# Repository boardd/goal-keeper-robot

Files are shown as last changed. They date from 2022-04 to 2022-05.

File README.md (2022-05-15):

# Autonomous Goal Keeper

## The Project

The aim of this project was to create a robot that can autonomously detect a "soccer ball" and defend a goal. We aimed to use computer vision for ball tracking and popular control methods such as PID and LQR to accurately position the robot's arm. After considering the relevant constraints such as time and cost, we decided to build a scale model of the setup so we can demonstrate the core capabilities of our robot without building a full scale version.

## The Robot

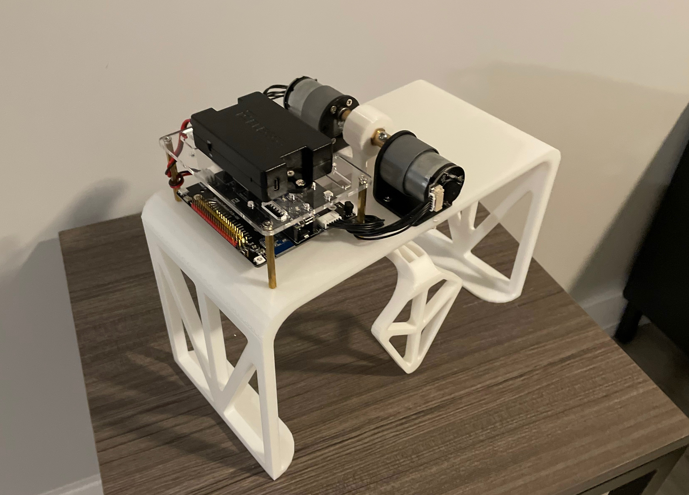
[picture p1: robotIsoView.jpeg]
Robot Isometric View


## The Hardware

The robot was constructed using 3D-Printed parts as this was the most efficient way for us to prototype and manufacture the robot. At first we wanted to use a stick shaped goalie to block balls but found that this would perform poorly for several reasons. A thin stick shaped goalie would require much more precise inverse kinematics which would be difficult for a project with such a short time frame. We would need a lot of control over the arm which would be difficult given the inconsistencies that could be present with our computer vision algorithm. A rectangular goal also proved difficult to cover for a single linked revolute arm as it only moves in one dimension, but needs to be able to defend the xy-plane formed by the front face of the robot. We eventually arrived at the design as shown in the picture below, which allowed us to cover the entire goal, including all of the corners. The goalie blocker also has cutouts so that we are able to optimize the rotational inertia and achieve larger accelerations by the motor.

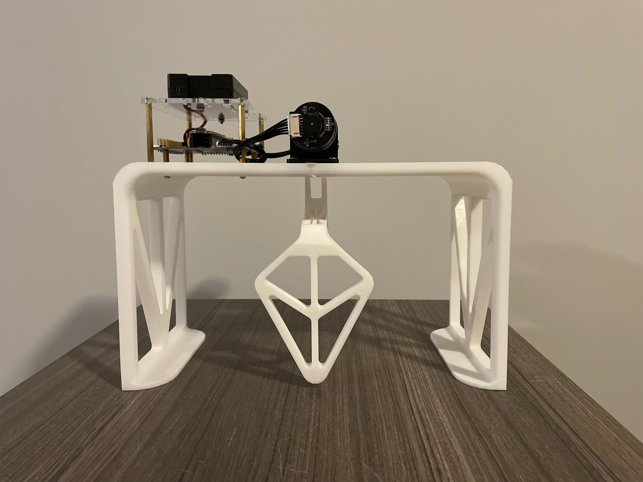
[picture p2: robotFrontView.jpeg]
Robot Front View


Most of the mounting hardware was recycled from the <a href="https://www.elegoo.com/collections/robot-kits/products/elegoo-tumbller-self-balancing-robot-car">Elegoo Tumbller</a>, which was the robot we used in labs in the past. This included 8 standoffs, 2 motor mounts, one plastic plate, and a few M3 screws. Although we designed the goal to be printed in 2 parts and glued together, we also used the motor mounts to strengthen the bridging by screwing it between the two halves. By mounting all of the hardware on top of the robot, we make the robot portable and easy to relocate to anywhere it might need to be. The two motors are set up in a counter-rotating configuration so that we are able to maximize the amount of availiable torque whilst still maintaining the maximum speed that we are able to reach. We chose to direct drive the motors as it was the most robust and simple design to implement given the time constraints.

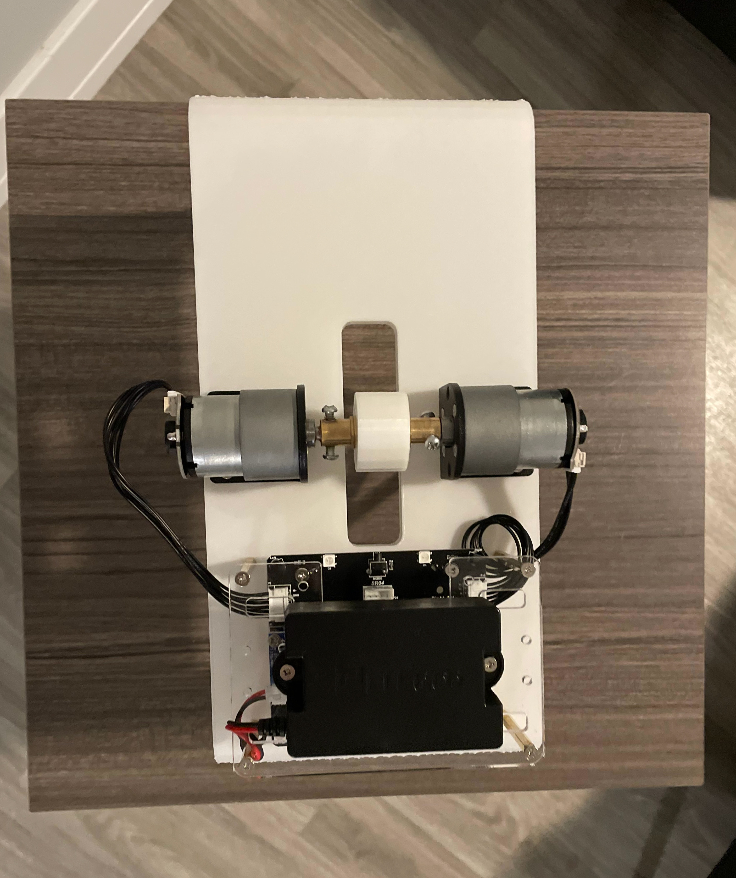
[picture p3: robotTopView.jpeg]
Robot Top View


### Electronics

The electronics of the robot are also mostly recycled from the Elegoo Tumbller. We used an Arduino Nano microcontroller to recieve and command joint positions to the two motors that came with the Elegoo kit. The motors have encoders which have 1560 ticks per revolution, enough resolution to allow us to have relatively high precision on the position of the motor. We also used the battery from the Elegoo kit to power our whole setup. A close up of our electronics is below.

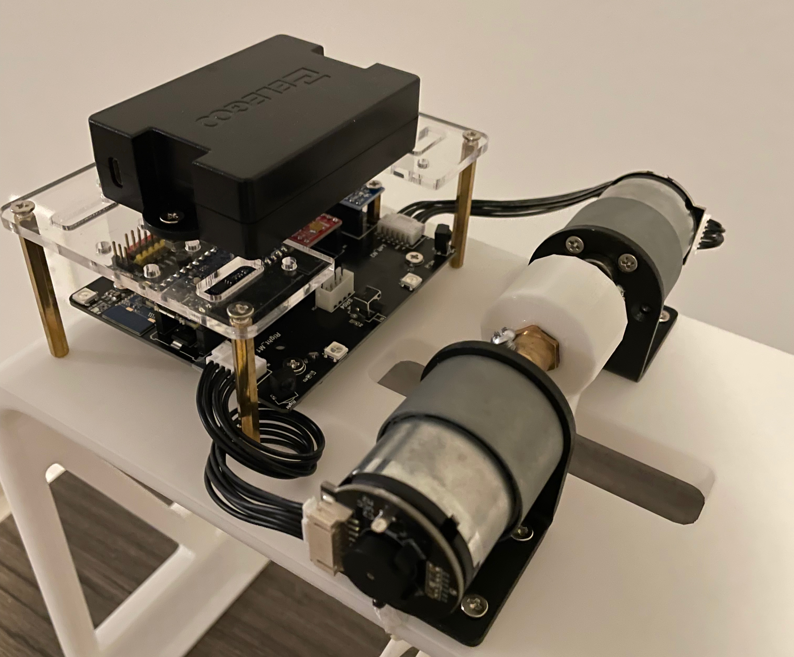
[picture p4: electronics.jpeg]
Electronics


Additionally, we used a camera rigged to provide a top view of the course as shown below. The camera uses a global shutter to minimize distortion and runs at roughly 37 fps. You can get the same camera <a href="https://www.amazon.com/Global-Shutter-Monochrome-Cameras-Windows/dp/B089QFRTVX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">here</a>, though we do recommend a different camera with a higher framerate if you able to get one. We light the scene using several lamps. This gives us much more controllable lighting conditions for thresholding in our computer vision.

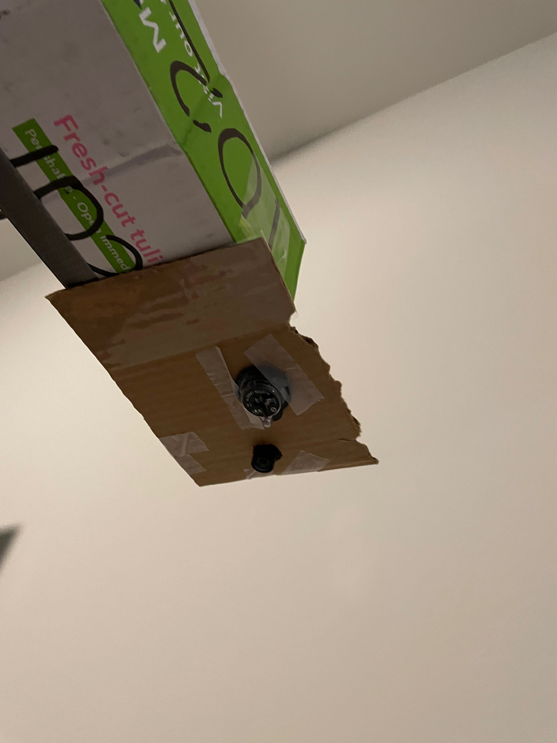
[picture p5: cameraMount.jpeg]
Camera Mount


### The Setup

We built the majority of the setup using cardboard. We first started by covering a large piece of cardboard with white paper to help our vision system more easily identify the ball. In hindsight, we would have used a color camera rather than a monochrome one as this made detecting the orange colored ping pong ball more difficult. We placed the camera roughly 5 feet above the ground so it is able to see most of the setup. We placed 4 ArUco markers in the corners of a rectangle to help our computer vision algorithm determine the location of the ball. Below are two pictures showing the full setup and what the view from the camera is roughly like (note that this was taken using a cell phone camera).

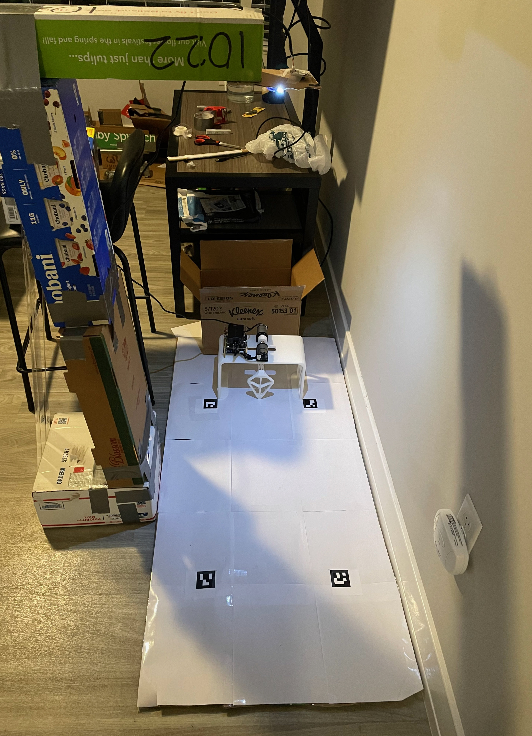
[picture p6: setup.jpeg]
Full Setup
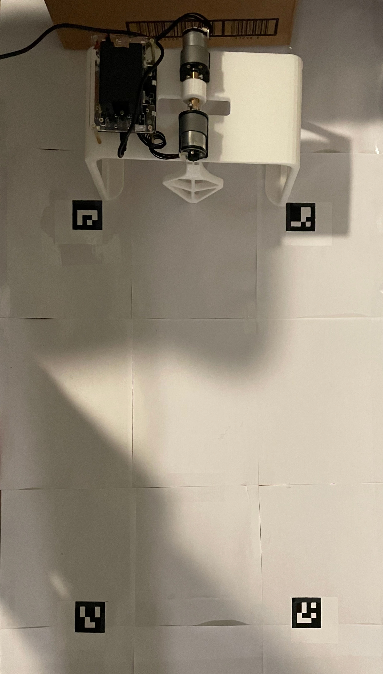
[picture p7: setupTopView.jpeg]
Top View of Setup
 

### Robot Dimensions

All dimensions are in millimeters.

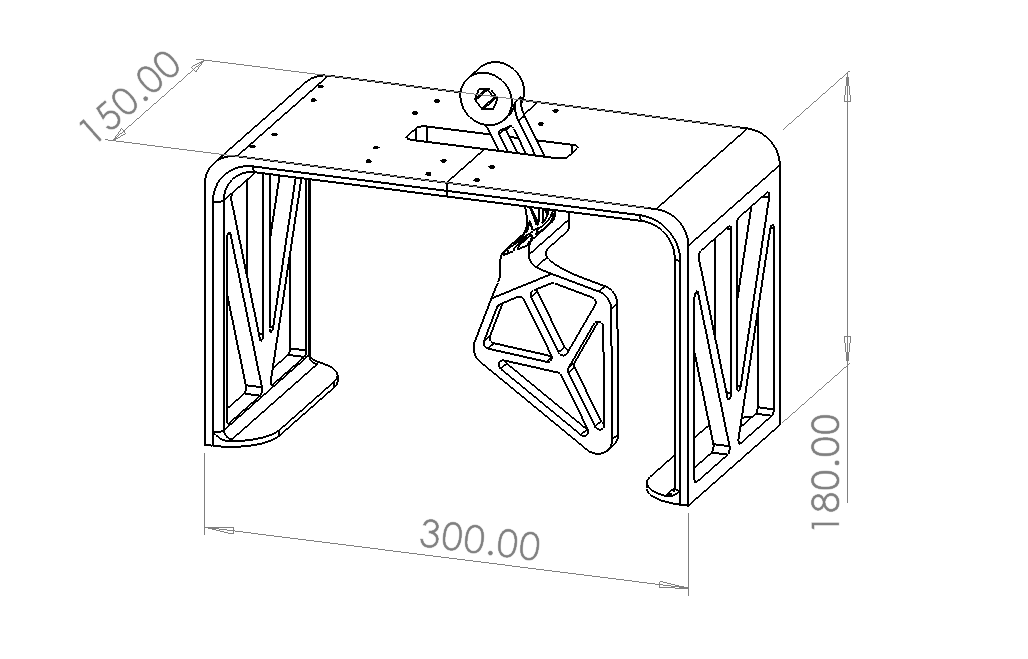
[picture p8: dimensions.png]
Robot Dimesions


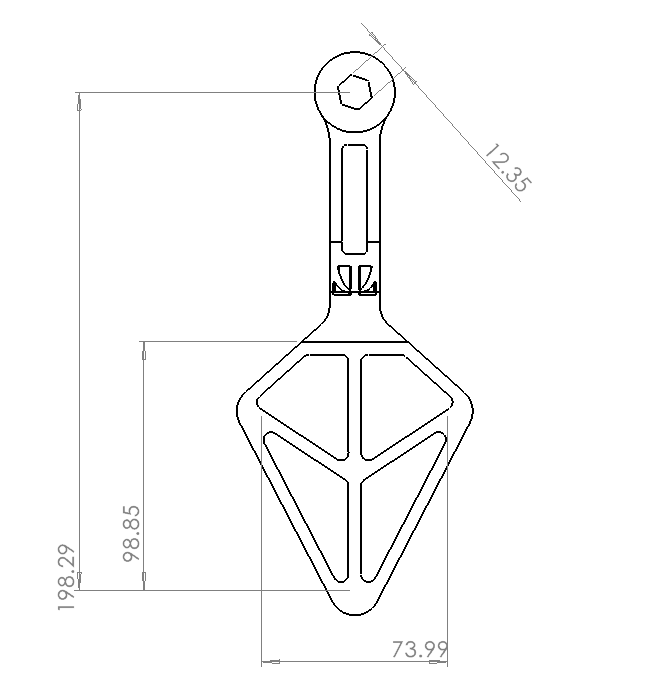
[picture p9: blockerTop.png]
Blocker Top Dimensions
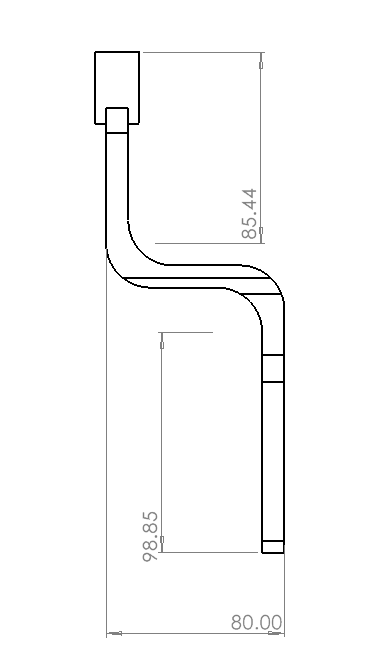
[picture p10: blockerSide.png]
Blocker Side Dimensions
 

### Robot CAD

All robot CAD is available on our github for 3D-printing (STL files only)

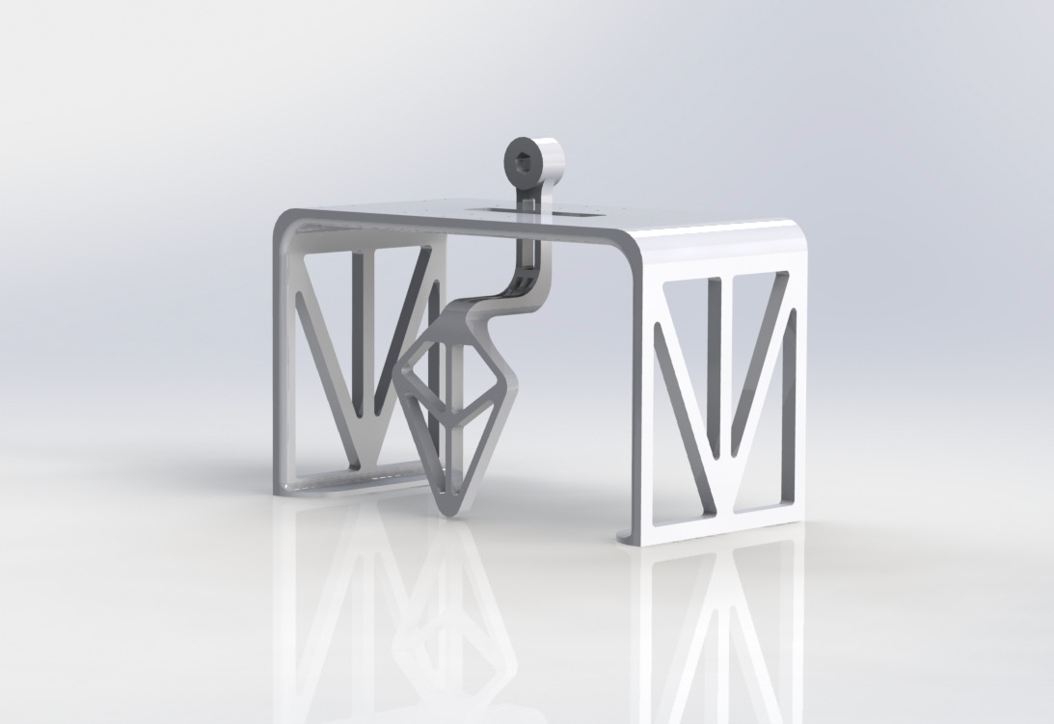
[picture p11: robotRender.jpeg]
robot render


### Parts Used

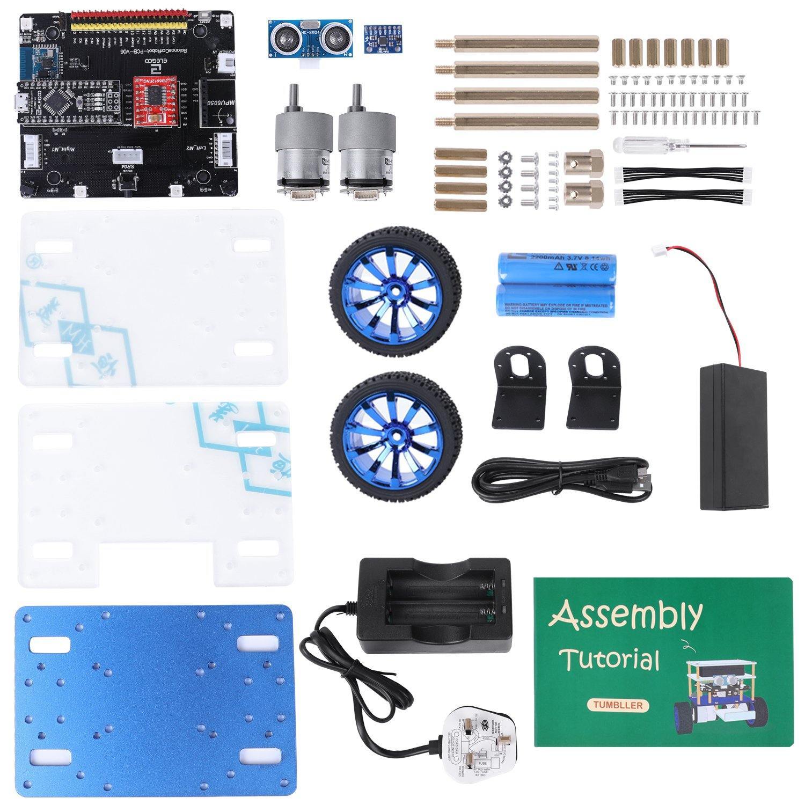
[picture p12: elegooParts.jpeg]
elegooParts
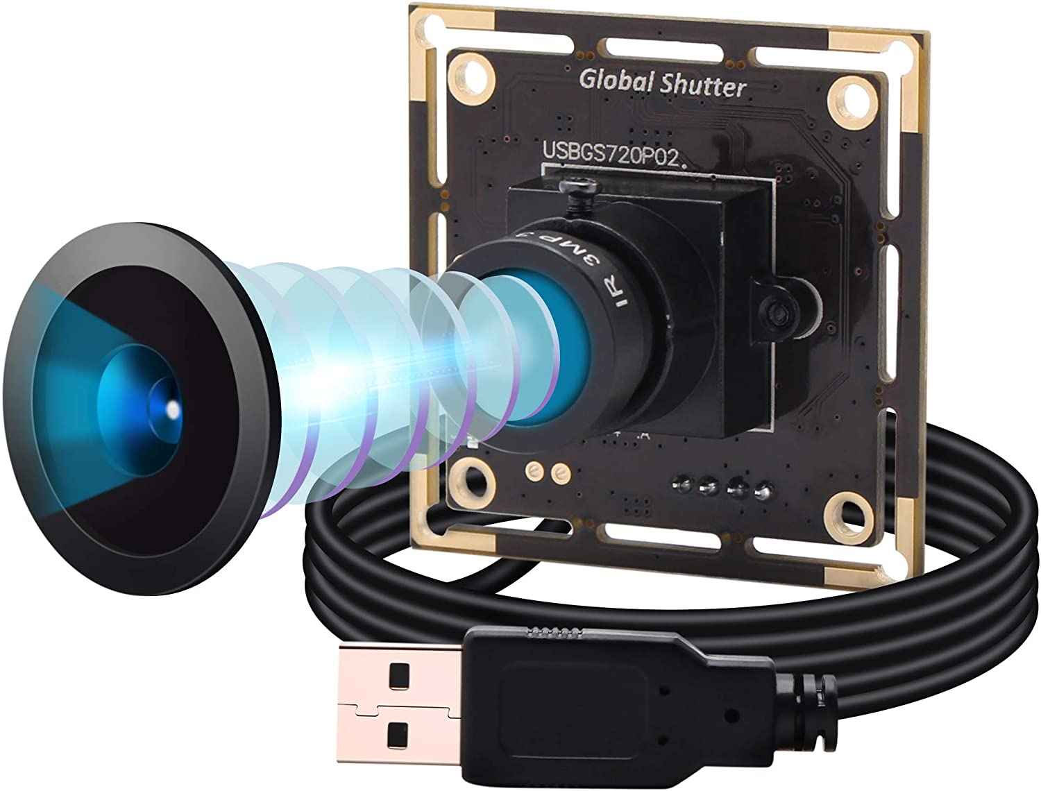
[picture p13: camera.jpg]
camera
 

## The Software

### Tracking the Ball

To compute the angle at which we should position the arm to block the ball, we need to know where the ball is going to end up in the horizontal direction, once it reaches the goal.

#### Finding the ball

We determine the location of the ball using a top down camera over the playing field. The raw images look like the following:

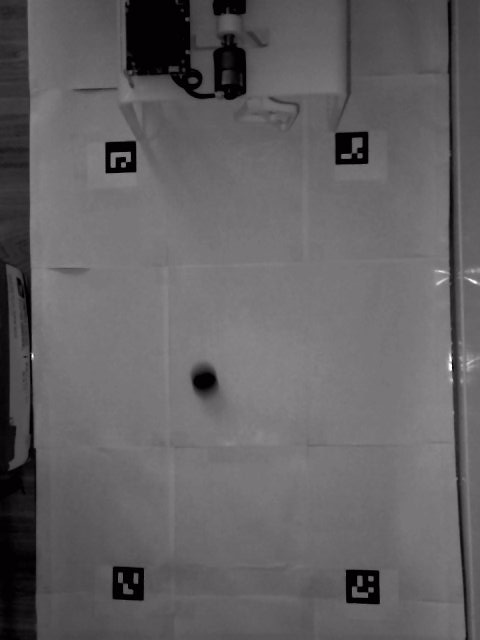
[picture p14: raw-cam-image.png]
Raw image from the camera


We painted the ball black to give it high contrast against the white playing field, which makes it easier to identify with computer vision. If you are not using a monochromatic camera like we did, you should be able to leave the ball its original color (orange) and you will find it much easier to threshold based on RGB or HSV values.

We use OpenCV to apply an adaptive gaussian threshold to the image, which yields the following:

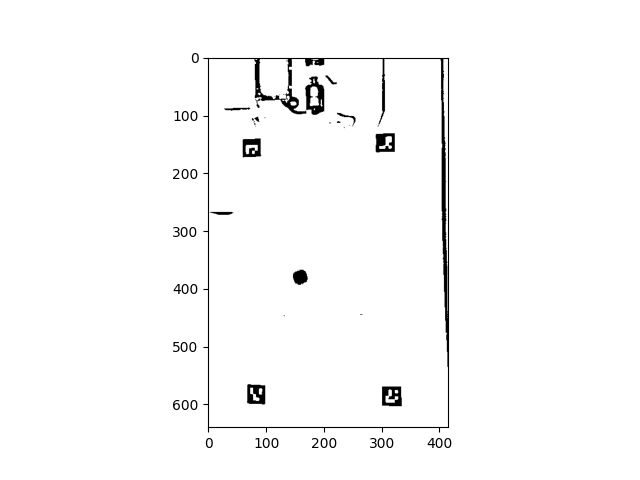
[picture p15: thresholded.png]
Thresholded image


We can then use OpenCV's contour detection to find contiguous regions of black pixels. We filter these contours by area, keeping only the ones within a pre-defined range. This helps us ignore contours that are too large or too small and reduces the number of false positives.

#### Computing the ball's position

Once we have identified one or more contours in the image, we can compute the position of each of these contours relative to the ArUco markers on the field, which are at known positions. We do so by using OpenCV's built-in ArUco marker detector. We can then compute a transformation from image space to world space and apply it to all of the identified contours.

Once we know the location of the contours in the real world, we can further filter them to exclude any which are not inside the rectangle defined by the markers. This reliably produces only a single location, corresponding to the ball.

In the following images, we draw a red rectangle with its center on where we believe the ball to be:

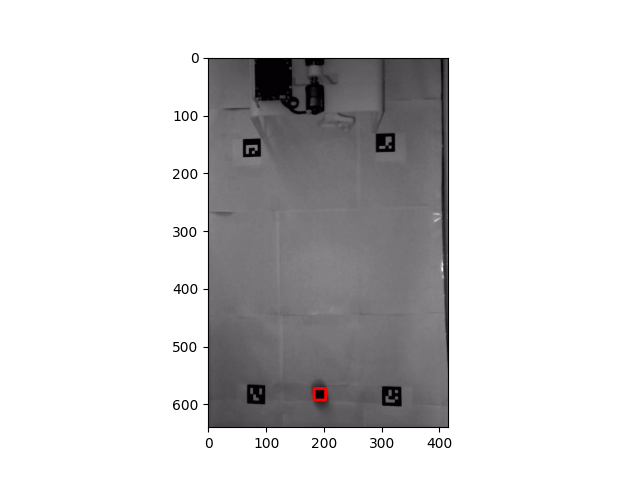
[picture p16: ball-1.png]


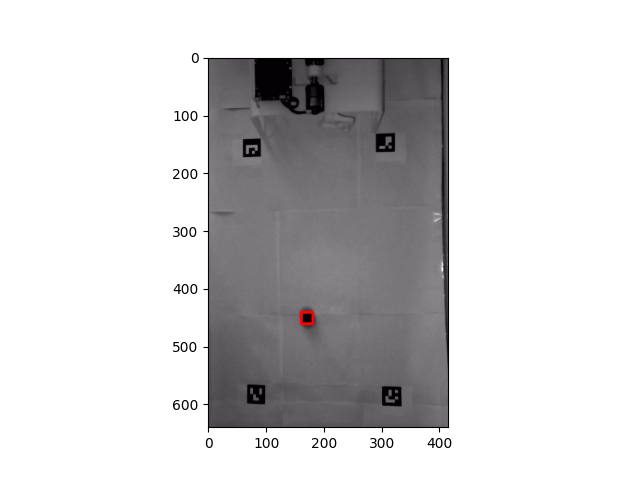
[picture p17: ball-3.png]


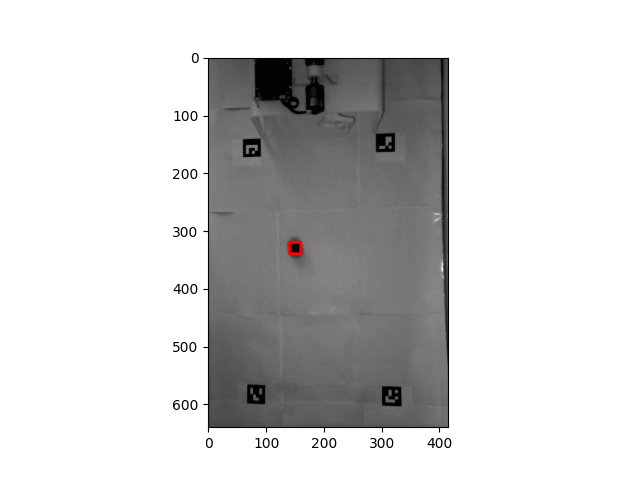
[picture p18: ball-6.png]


#### Estimating the ball's trajectory

Once we have the position of the ball over several frames, we can estimate its trajectory in order to predict where it will end up when it reaches the goal. If we only have a single frame of the ball so far, we simply use its x-coordinate in world space. Otherwise, we take up to the last 5 positions of the ball, and for each subsequent pair of positions, compute the velocity of the ball in world space. We take the average of these velocities, then solve for the ball's x-coordinate at the time that it would reach the y-coordinate of the goal. The following video visualizes this computation:

<iframe width="560" height="315" src="https://www.youtube.com/embed/EhwE5aTzZk0" title="YouTube video player" frameborder="0" allow="accelerometer; autoplay; clipboard-write; encrypted-media; gyroscope; picture-in-picture" allowfullscreen></iframe>

### LQR Control

We control the arm with an LQR controller, using the following linear model of the dynamics. Constant c0 represents a friction term, and constant c1 represents the impact of the control sent to the motor on its velocity.

A Matrix

B Matrix

We collected data by sending a sequence of commands to the robot and measuring the resulting angles over time. We then tuned constants c0 and c1 to match this data, which yielded c0=.03, c1=.00285. The following is a plot comparing the actual encoder data after a sequence of commands with a simulation using the above model and parameters.

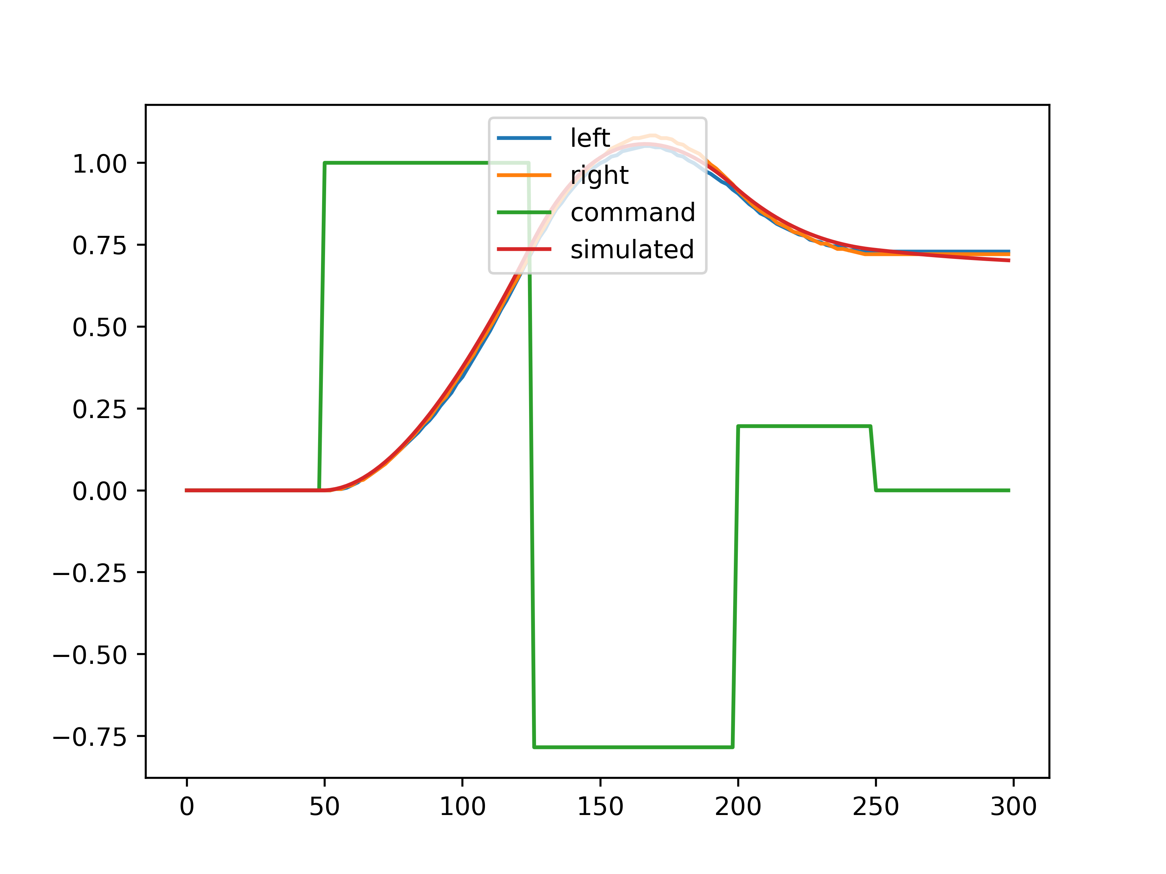
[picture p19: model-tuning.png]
Graph of model tuning vs real data


### Communication

Since the arm of the goal keeping robot is controlled by an arduino, it cannot read the images from the camera directly. Instead, our computer vision algorithm runs on a laptop connected to the USB camera as well as the arduino, over serial. The laptop reads images from the camera, computes the location of the ball on the board, computes the angle at which the arm should be set, and finally sends that desired angle over the serial port to the arduino. We used pyserial to establish the serial communications between the arduino and the computer. Upon receiving an update, the arduino LQR controller issues commands to the motors to achieve the desired angle.

## Performance Demonstrations

Below are some youtube videos showing how our robot performs under different circumstances.

### Ball on Stick

<iframe width="560" height="315" src="https://www.youtube.com/embed/wQ2Xh3evgs4" title="YouTube video player" frameborder="0" allow="accelerometer; autoplay; clipboard-write; encrypted-media; gyroscope; picture-in-picture" allowfullscreen></iframe>

### Without trajectory estimation

<iframe width="560" height="315" src="https://www.youtube.com/embed/va0qUtZI4oE" title="YouTube video player" frameborder="0" allow="accelerometer; autoplay; clipboard-write; encrypted-media; gyroscope; picture-in-picture" allowfullscreen></iframe>

### With trajectory estimation

<iframe width="560" height="315" src="https://www.youtube.com/embed/xyy4dbmpT3A" title="YouTube video player" frameborder="0" allow="accelerometer; autoplay; clipboard-write; encrypted-media; gyroscope; picture-in-picture" allowfullscreen></iframe>

## Problems Faced

### Communication

#### The Problem

One issue we faced is that when we rapidly sent updates to the desired angle to the LQR controller, we observed unpredictable behavior. The following is a video in which we sent updates with a 0.2s delay in-between. The robot behaved as expected:

<iframe width="560" height="315" src="https://www.youtube.com/embed/YelFhvKkZ9k" title="YouTube video player" frameborder="0" allow="accelerometer; autoplay; clipboard-write; encrypted-media; gyroscope; picture-in-picture" allowfullscreen></iframe>

However, if we sent updates more rapidly, the controller behaved unexpectedly. The following is a video in which we sent the updates with a 0.1s delay:

<iframe width="560" height="315" src="https://www.youtube.com/embed/VBRqGhC0dmI" title="YouTube video player" frameborder="0" allow="accelerometer; autoplay; clipboard-write; encrypted-media; gyroscope; picture-in-picture" allowfullscreen></iframe>

#### The Solution

Initially, we thought this may be a quirk of the LQR controller which we were using. However, it turned out that as we sent several updates over serial in rapid succession, the messages would be read simultaneously on the Arduino side. This yielded a garbled desired angle, which caused the unpredictable behavior. We solved the issue by separating each update to the arduino with a line break '\n'. On the Arduino side, we could then use the Serial.readStringUntil('\n') method to isolate each update appropriately.

### Lag

#### The Problem

As with any digital system, there is significant latency from the balls motion in the real world to the camera producing an image, to the computer vision system producing a position, and to the arduino finally positioning the arm. This sequence of delays meant that the arm could not quite keep up with the ball, which caused the arm to miss if the ball was travelling diagonally.

#### The Solution

As discussed above, the solution to this problem was to rely not on our computation of where the ball is currently, but to also predict where the ball will be in the future. Although the system is not able to react any faster, it can make a smarter decision on where to position the arm. Adding trajectory estimation increased the success rate of the arm from around 60% to more than 95%.

## Future Work

### 3D

Currently, the goal keeper only operates in two dimensions. It has no knowledge of the ball's height relative to the ground. With an additional camera looking at the board sideways, we could incorporate this information to better inform the arm's position.

### Scale

Bigger is better. We chose to make a relatively small robot for the sake of simplicity given the limited time we had to develop the system. A larger robot (even full-scale) would of course introduce challenges with safety, overcoming inertia, and overcoming additional inaccuracies given a smaller margin of error.

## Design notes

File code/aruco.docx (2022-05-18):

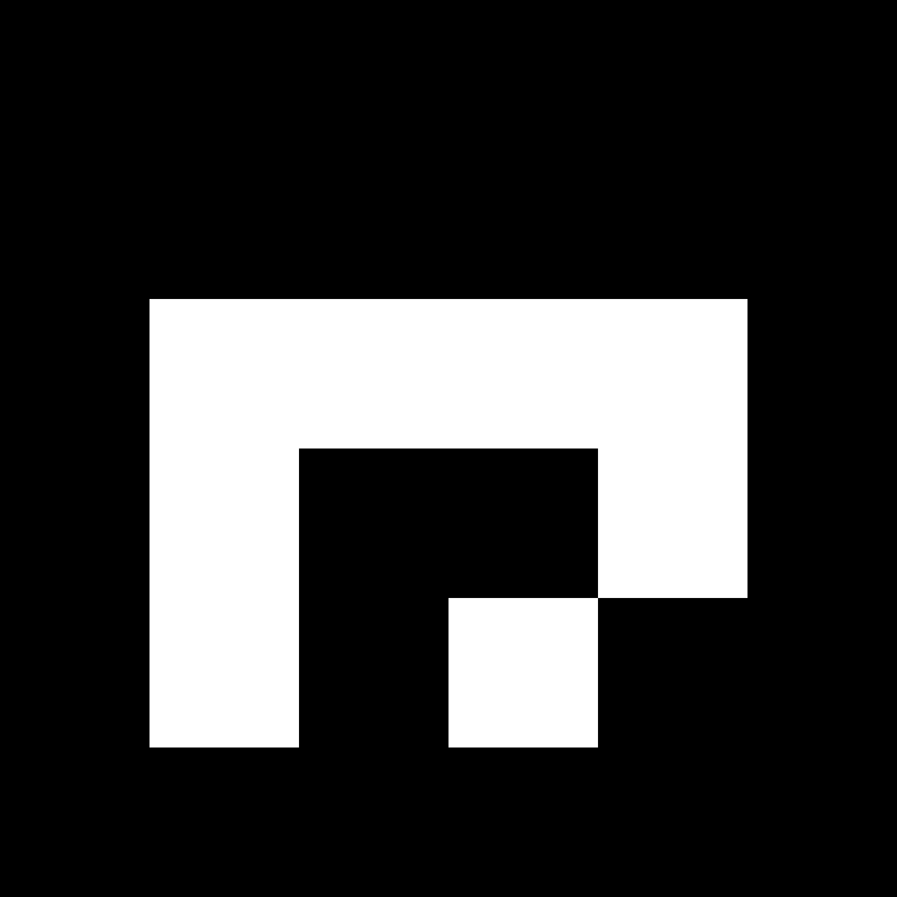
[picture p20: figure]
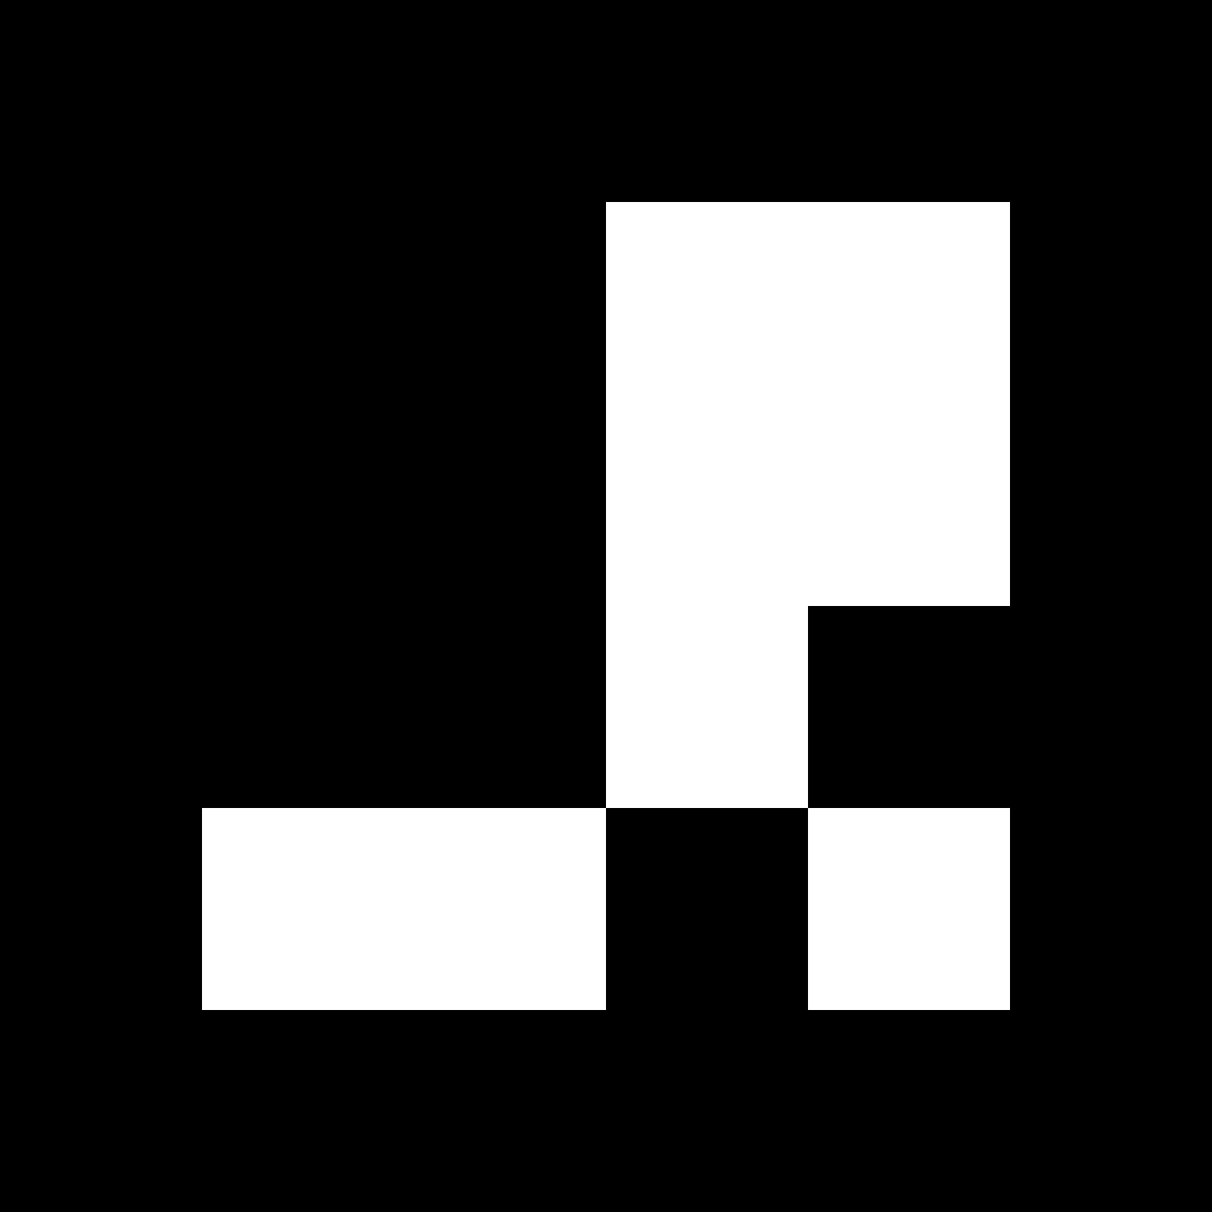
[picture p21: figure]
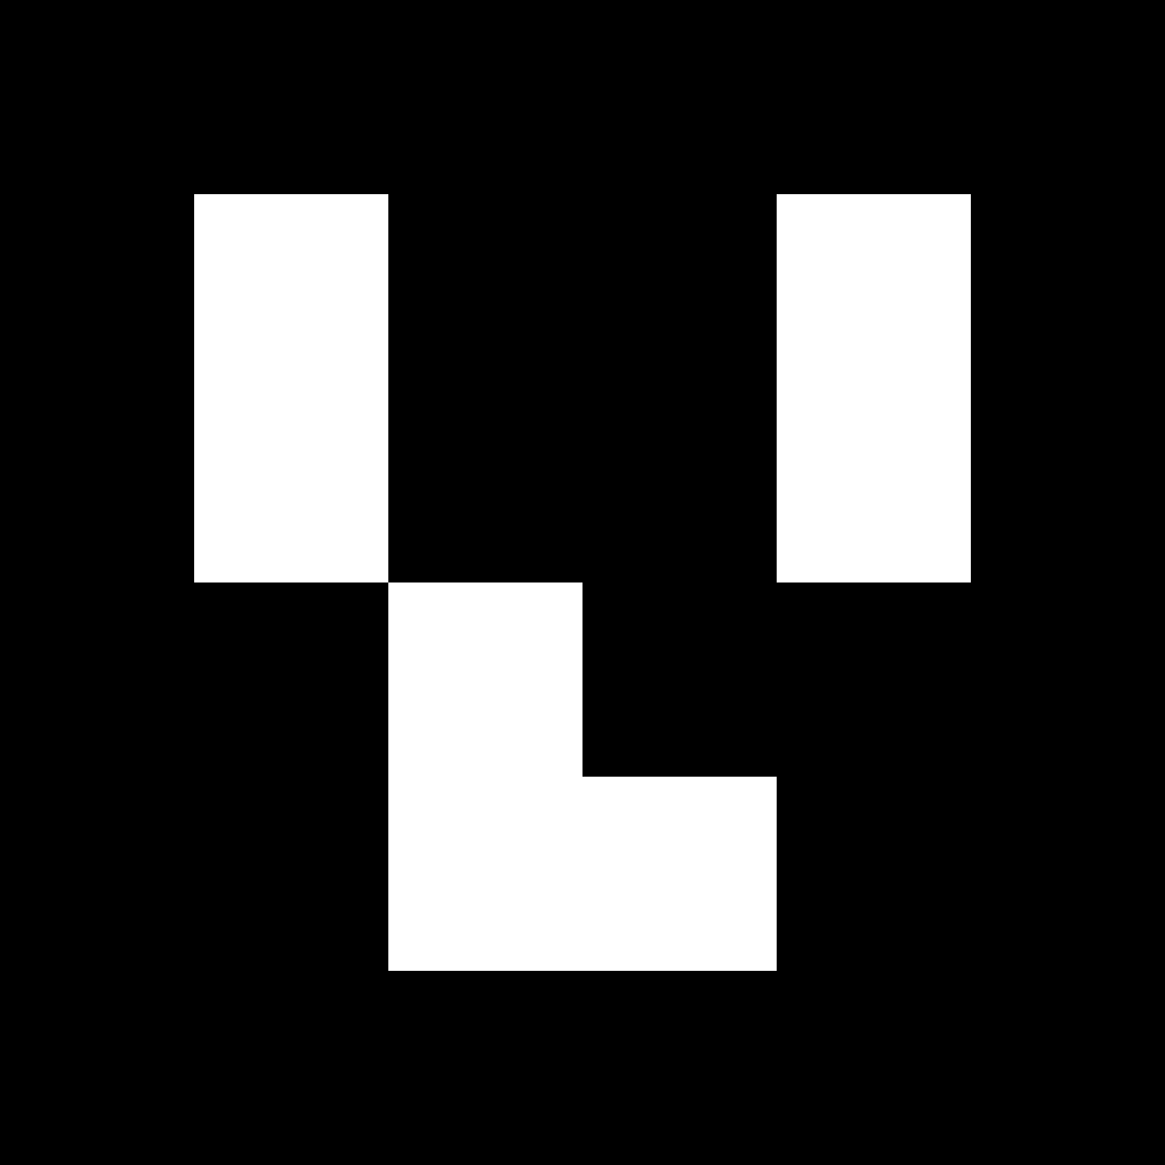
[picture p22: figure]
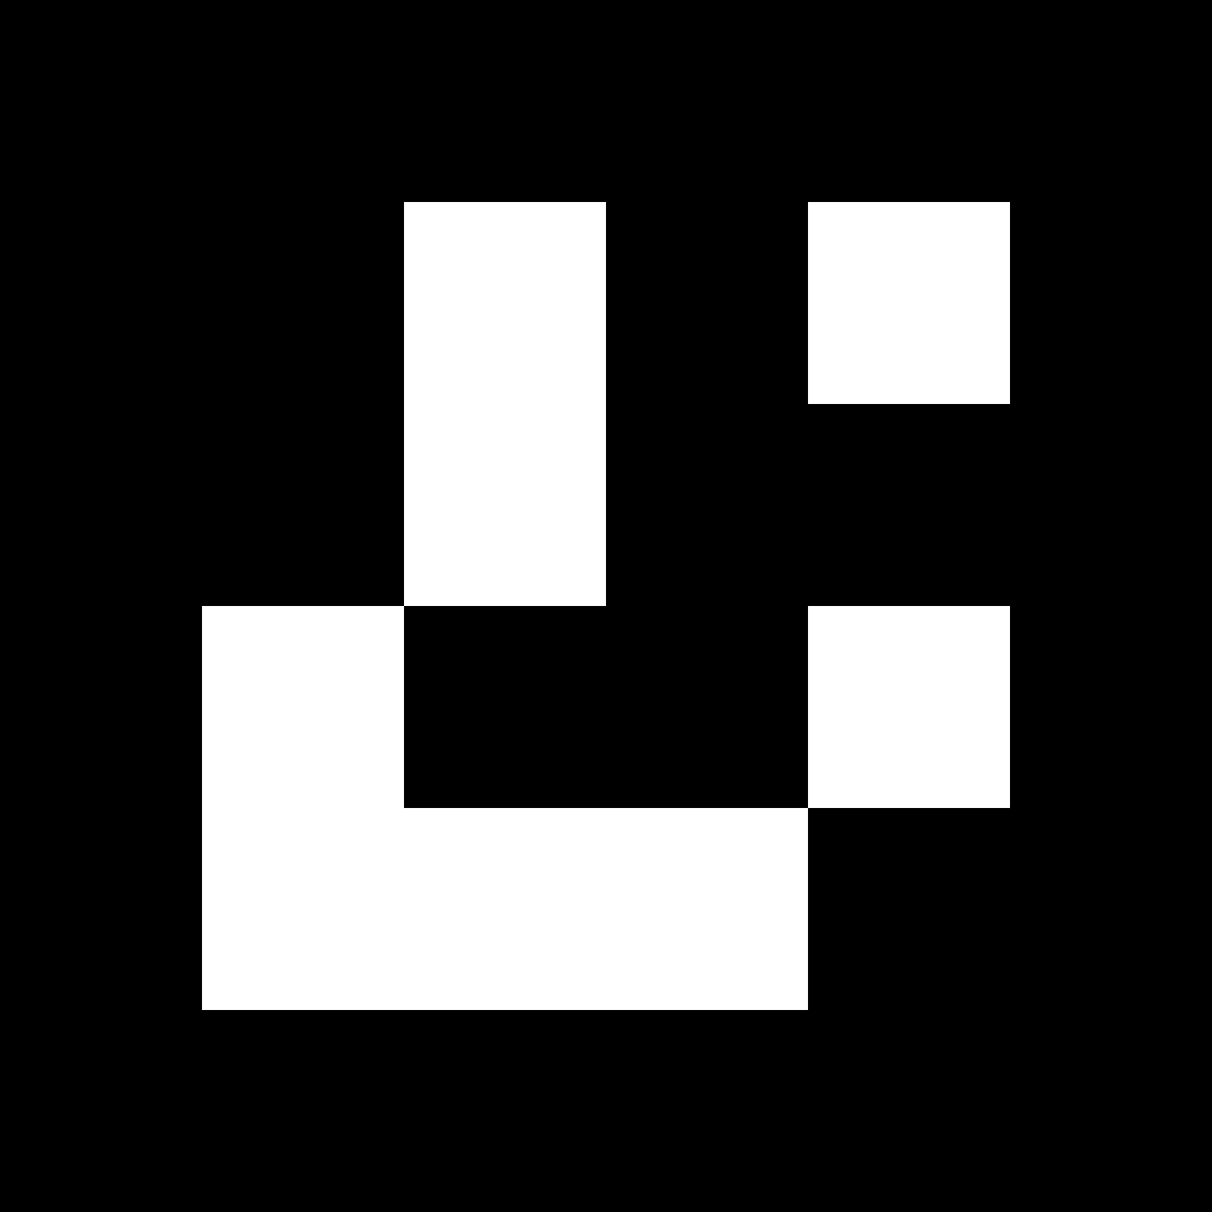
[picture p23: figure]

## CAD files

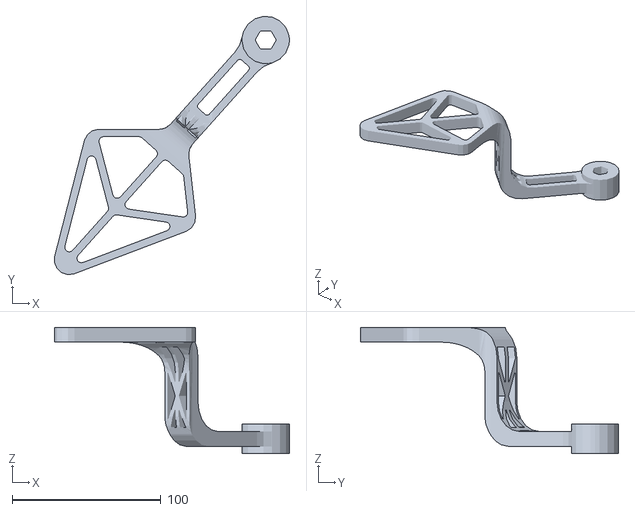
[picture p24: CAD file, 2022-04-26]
Printable Files/blocker arm.STL
158.0 x 173.7 x 85.0

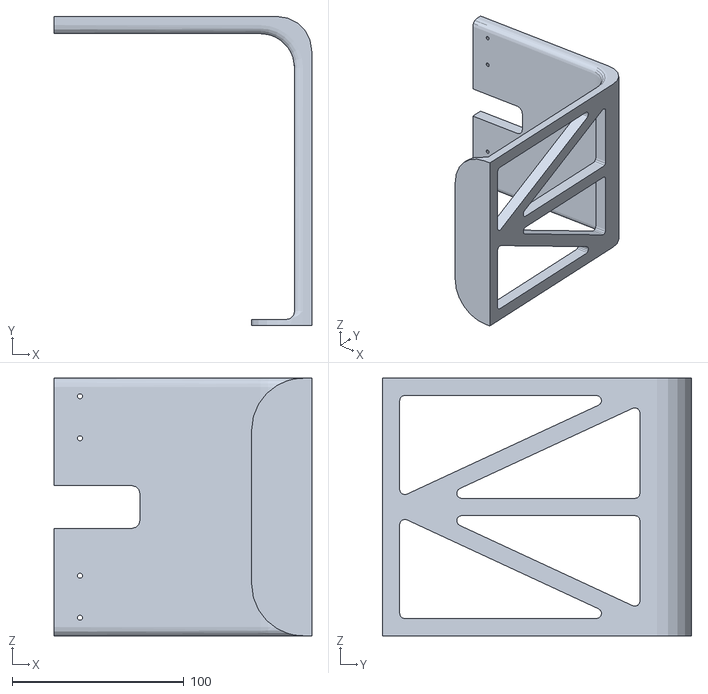
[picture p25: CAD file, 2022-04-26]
Printable Files/goal-right.STL
150.0 x 180.0 x 150.0

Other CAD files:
Printable Files/goal-left.STL

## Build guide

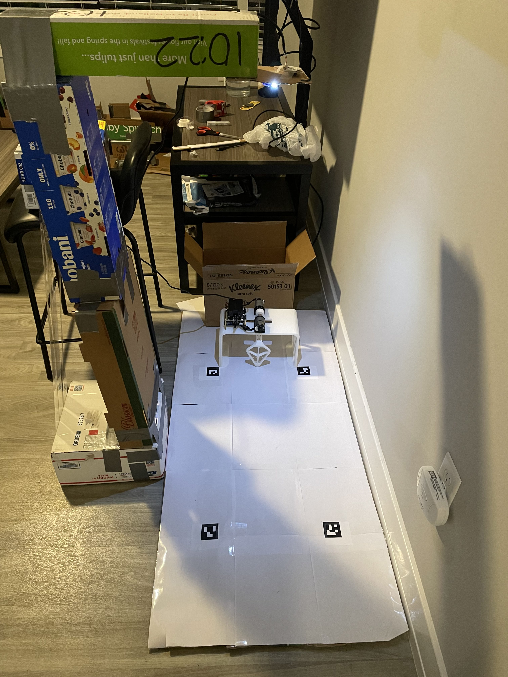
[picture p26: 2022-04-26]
setup.jpg

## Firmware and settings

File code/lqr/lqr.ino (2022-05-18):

/******************************************************************/

#include "my_encoders.h"
#include "Motor.h"

/******************************************************************/

Motor Motor;

void setup()
{
  Serial.begin( 1000000 );
  while ( !Serial ) {};
  Serial.setTimeout(100);
  Motor.Motor_init();
  Encoder_init( &(Motor.left_angle), &(Motor.right_angle) );
}

float k1 = 960;
float k2 = 28.5;
float ts = 0.002;
float MAX_ANGLE = 0.6;

/******************************************************************/

bool VERBOSE = false;
unsigned long start_micros = -1;
unsigned long timestep_micros = 2000;
unsigned long next_timestep_micros = -1;

void loop()
{
  Encoder_init( &(Motor.left_angle), &(Motor.right_angle) );
  start_micros = micros();
  next_timestep_micros = 0;
  float previous_angle_radians = 0;
  float desired_angle_radians = 0;
  Serial.println("READY");
  while (true) {
    if ( Serial.available() > 0 ) {
      String s = Serial.readStringUntil('\n');
      char *cmd = s.c_str();
      if (VERBOSE) {
        Serial.print("Received: ");
        Serial.println(cmd);
      }
      if (cmd[0] == 'v') {
        VERBOSE = !VERBOSE;
      } else {
        desired_angle_radians = atof(cmd);
        if (desired_angle_radians > MAX_ANGLE) {
          desired_angle_radians = MAX_ANGLE;
        }
        if (desired_angle_radians < -MAX_ANGLE) {
          desired_angle_radians = -MAX_ANGLE;
        }
      }
    }

    unsigned long current_micros = micros();
    unsigned long elapsed_micros = current_micros - start_micros;
    unsigned long elapsed_millis = elapsed_micros / 1000;

    // Timekeeping
    if (elapsed_micros < next_timestep_micros) {
      continue;
    }
    next_timestep_micros += timestep_micros;

    // Read encoders
    Read_encoders( &(Motor.left_angle), &(Motor.right_angle) );

    // Compute angle and velocity
    float current_angle_encoder = ((float)Motor.left_angle + (float)Motor.right_angle) / 2.0;
    float current_angle_radians = current_angle_encoder / 780.0 * PI;
    float current_velocity_radians = (current_angle_radians - previous_angle_radians) / ts;
    previous_angle_radians = current_angle_radians;

    // Do LQR
    float desired_velocity = 0;

    float current_error_radians = desired_angle_radians - current_angle_radians;
    float current_velocity_error = desired_velocity - current_velocity_radians;

    long command = k1 * current_error_radians + k2 * current_velocity_error;

    // Safety
    if (command > 255) {
      command = 255;
    }
    if (command < -255) {
      command = -255;
    }

    // Logging
    if (VERBOSE) {
      Serial.print("elapse:");
      Serial.println(elapsed_micros);
      Serial.print("angle:");
      Serial.println(current_angle_radians);
      Serial.print("vel:");
      Serial.println(current_velocity_radians);
      Serial.print("des angle:");
      Serial.println(desired_angle_radians);
      Serial.print("des vel:");
      Serial.println(desired_velocity);
      Serial.print("cmd:");
      Serial.println(command);
      Serial.println("-----");
    }

    Motor.Left_command(command);
    Motor.Right_command(command);
  }

  Motor.Stop();
}

/******************************************************************/

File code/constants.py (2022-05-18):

ARM_HEIGHT = 8 + (3 / 8)  # inches

AREA_MIN = 400
AREA_MAX = 1200

EXPECTED_HEIGHT_OVER_WIDTH = 1
MAX_HEIGHT_OVER_WIDTH_ERROR = 2

# Aruco marker positions
# 1 2
# 3 4
ARUCO_MARKER_SIZE = 2  # width/height, inches
BOARD_WIDTH = 14  # Distance between centers horizontally, inches
BOARD_HEIGHT = 26  # Distance between centers vertically, inches
BOARD_MARGIN = ARUCO_MARKER_SIZE / 2

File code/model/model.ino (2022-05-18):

/******************************************************************/

#include "my_encoders.h"
#include "Motor.h"

/******************************************************************/

#define TARGET 500

/******************************************************************/

Motor Motor;

static bool go = false;  /* motor enable */

/******************************************************************/

void setup()
{
  Serial.begin( 1000000 );
  while( !Serial ){};
  delay( 1000 ); // Delay to make sure above message prints out.
  Motor.Motor_init();
  Serial.println( "Motor.Pin_init done." );
  Serial.println( "If we hang here power cycle the robot. Expect more printout" );
  delay( 1000 ); // Delay to make sure above messages print out.
  Encoder_init( &(Motor.left_angle), &(Motor.right_angle) );
  Serial.println( "Encoder_init done." );
  Serial.println( "Wheels should be off the ground."  );
  Serial.println( "Type g <return> to run test, s <return> to stop."  );
  Serial.println( "Typing window is at the top of the serial monitor window" );
}

/******************************************************************/

// Take user input
void ProcessCommand()
{

  if ( Serial.available() <= 0 )
    return;

  int c = Serial.read();
  switch (c)
    {
      case 'S': case 's':
        Serial.println( "Stop!" );
        go = false;
        break;
      case 'G': case 'g':
      Serial.println( "Go!" );
        go = true;
        break;
      default:
        break;
    }
}

/******************************************************************/

unsigned long start_micros = -1;
unsigned long timestep_micros = 2000;
unsigned long next_timestep_micros = -1;

void loop()
{
  if (!go) {
    start_micros = -1;
    next_timestep_micros = -1;
    Motor.Stop();
    ProcessCommand();
    return;
  }

  if (start_micros == -1) {
    start_micros = micros();
    next_timestep_micros = 0;
  }

  unsigned long current_micros = micros();
  unsigned long elapsed_micros = current_micros - start_micros;
  unsigned long elapsed_millis = elapsed_micros / 1000;

  // Reset
  if (elapsed_millis >= 300) {
    Encoder_init( &(Motor.left_angle), &(Motor.right_angle) );
    go = false;
    Motor.Stop();
    return;
  }

  if (elapsed_micros < next_timestep_micros) {
    return;
  }
  next_timestep_micros += timestep_micros;  

  int command = 0;

  if (elapsed_millis >= 0) {
    command = 0;
  }
  if (elapsed_millis >= 50) {
    command = 255;
  }
  if (elapsed_millis >= 125) {
    command = -200;
  }
  if (elapsed_millis >= 200) {
    command = 50;
  }
  if (elapsed_millis >= 250) {
    command = 0;
  }

  Motor.Left_command( command );
  Motor.Right_command( command );

  Read_encoders( &(Motor.left_angle), &(Motor.right_angle) );

  Serial.print(elapsed_millis);
  Serial.print(",");
  Serial.print(Motor.left_angle);
  Serial.print(",");
  Serial.print(Motor.right_angle);
  Serial.print(",");
  Serial.print(command);
  Serial.println("");
}

/******************************************************************/

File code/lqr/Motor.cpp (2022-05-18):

#include <Arduino.h>
#include "Motor.h"

/* Motor pins */
#define AIN1 7
#define PWMA_LEFT 5
#define BIN1 12
#define PWMB_RIGHT 6
#define STBY_PIN 8

void Motor::Motor_init()
{
  pinMode(AIN1, OUTPUT);
  pinMode(BIN1, OUTPUT);
  pinMode(PWMA_LEFT, OUTPUT);
  pinMode(PWMB_RIGHT, OUTPUT);
  digitalWrite(AIN1, HIGH);
  digitalWrite(BIN1, LOW);
  analogWrite(PWMA_LEFT, 0);
  analogWrite(PWMB_RIGHT, 0);
  pinMode(STBY_PIN, OUTPUT);
  digitalWrite(STBY_PIN, HIGH);
}

void Motor::Stop()
{
  digitalWrite(AIN1, HIGH);
  digitalWrite(BIN1, LOW);
  analogWrite(PWMA_LEFT, 0);
  analogWrite(PWMB_RIGHT, 0);
}

void Motor::Forward(int speed)
{
  digitalWrite(AIN1, 0);
  digitalWrite(BIN1, 0);
  analogWrite(PWMA_LEFT, speed);
  analogWrite(PWMB_RIGHT, speed);
}

void Motor::Back(int speed)
{
  digitalWrite(AIN1, 1);
  digitalWrite(BIN1, 1);
  analogWrite(PWMA_LEFT, speed);
  analogWrite(PWMB_RIGHT, speed);
}


void Motor::Left(int speed)
{
  digitalWrite(AIN1, 1);
  digitalWrite(BIN1, 1);
  analogWrite(PWMA_LEFT, speed);
  analogWrite(PWMB_RIGHT, 0);
}

void Motor::Right(int speed)
{
  digitalWrite(AIN1, 1);
  digitalWrite(BIN1, 1);
  analogWrite(PWMA_LEFT,0);
  analogWrite(PWMB_RIGHT,speed);
}

void Motor::Left_command(int speed)
{
    if ( speed >= 0 )
    {
      digitalWrite( AIN1, 1 );
      analogWrite( PWMA_LEFT, speed );
    }
  else
    {
      digitalWrite( AIN1, 0 );
      analogWrite( PWMA_LEFT, -speed );
    }
}

// reverses the sign of "speed"
void Motor::Right_command( int speed )
{
  if ( speed >= 0 )
    {
      digitalWrite( BIN1, 1 );
      analogWrite( PWMB_RIGHT, speed );
    }
  else
    {
      digitalWrite( BIN1, 0 );
      analogWrite( PWMB_RIGHT, -speed );
    }
}

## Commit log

2022-04-26 Added some printable STL files
2022-05-15 Remove part about single motor
